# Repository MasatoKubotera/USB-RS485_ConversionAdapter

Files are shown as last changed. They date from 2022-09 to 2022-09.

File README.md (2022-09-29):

<html lang="en">
  <head>
    <meta charset="uft-8">
    <meta name="author" content="Masato Kubotera">
  </head>
  <body>
    <h1>USB-RS485 Conversion Adapter Ver. 2.1</h1>
    <h2>About USB-RS485 Conversion Adapter</h2>
    <p>
      The USB-RS485 Conversion Adapter converts communications from the USB interface to the RS-485 interface and can drive KONDO B3M series servo motors.<br>
      <br>
      Note that this is Ver. 2.1. For other versions, please refer to the following repositories.
      <ul>
        <li><a href="https://github.com/MasatoKubotera/USB-RS485_ConversionAdapter_ver2_0">USB-RS485 Conversion Adapter Ver. 2.0</a></li>
      </ul>
      <h2>About Ver. 2.1</h2>
      Ver. 2.1 has a switch and four indicator LEDs to turn the power supply for driving servo motors on and off on the board.
      <!--
      Ver.2.1では、サーボモーター駆動用の電源を基板上でON/OFFするためのスイッチと4つのインジケーターLEDを搭載しています。
      -->
      <table>
        <tr>
          <td>
            <a href="image/brd_top.png">
              <div align="center">
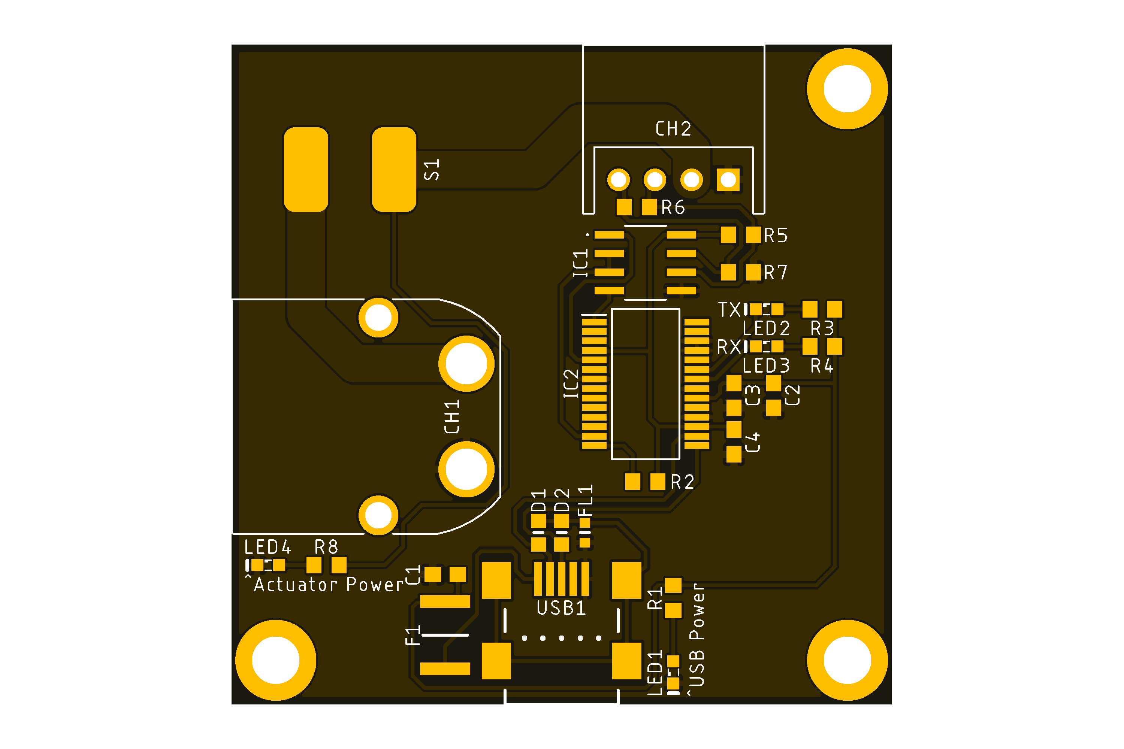
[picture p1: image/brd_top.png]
                
              </div>
            </a>
          </td>
          <td>
            <div align="center">
              
            </div>
          </td>
          <td>
            <div align="center">
              
            </div>
          </td>
        </tr>
        <tr>
          <td>
            <div align="center">
              PCB preview image
            </div>
          </td>
          <td>
            <div align="center">
              Actual PCB
            </div>
          </td> 
          <td>
            <div align="center">
              After component mounting
            </div>
          </td>   
        </tr>
      </table>
    </p>
    <h2>Repository Contents</h2>
    <p>
    <dl>
      <dt>\image</dt>
      <dd>PCB preview images and capture of design screen</dd>
      <dt>\libraries</dt>
      <dd>Libraries used in Autodesk Eagle design</dd>
      <dt>Schematic.pdf</dt>
      <dd>Circuit diagram of this product</dd>
      <dt>BOM.txt</dt>
      <dd>Parts lists output from design data</dd>
      <dt>.brd</dt>
      <dd>Board wiring design file by Autodesk Eagle</dd>
      <dt>.sch</dt>
      <dd>Schematic design file by Autodesk Eagle</dd>
      <dt>Gerber_data.zip</dt>
      <dd>Zip folder of Gerber format files for PCB manufacturing requests.</dd>
      <dt>LICENSE</dt>
      <dd>This is a license to use this product. Please confirm before use.</dd>
      <dt>.gitignore</dt>
      <dd>File to exclude cache files from management.</dd>
    </dl>
    </p>
    <h2>Documentation</h2>
      <p>
        <h3>BOM</h3>
          <table>
            <thead>
              <tr>
                <th> Eagle Design Parts # </th>
                <th> Q'ty </th>
                <th> Mfr. Product # </th>
                <th> Supplier </th>
                <th> Description </th>
              </tr>
            </thead>
            <tbody>
              <tr>
                <td> LED1, LED4 </td>
                <td> 2 </td>
                <td> 150060VS86000 </td>
                <td> <a href="https://www.mouser.jp/ProductDetail/Wurth-Elektronik/150060VS86000?qs=GedFDFLaBXGW9qOjzZ1Hmw%3D%3D">Mouser</a> </td>
                <td> Standard LEDs - SMD Green 2V 20mA 573nm 0603 </td>
              </tr>
              <tr>
                <td> LED2, LED3 </td>
                <td> 2 </td>
                <td> 150060YS75000 </td>
                <td> <a href="https://www.mouser.jp/ProductDetail/Wurth-Elektronik/150060YS75000?qs=LlUlMxKIyB0nKmwefHgtZw%3D%3D">Mouser</a> </td>
                <td> Standard LEDs - SMD Yellow 2V 20mA 590nm 0603 </td>
              </tr>
              <tr>
                <td> FL1 </td>
                <td> 1 </td>
                <td> BLM18SD220SN1D </td>
                <td> <a href="https://www.mouser.jp/ProductDetail/Murata-Electronics/BLM18SD220SN1D?qs=glnLrWX4TPq%2Fm8%2FdPQltLg%3D%3D">Mouser</a> </td>
                <td> Ferrite Beads 22 OHM 0603 </td>
              </tr>
              <tr>
                <td> R1, R3, R4 </td>
                <td> 3 </td>
                <td> RC0603FR-101KL </td>
                <td> <a href="https://www.mouser.jp/ProductDetail/YAGEO/RC0603FR-101KL?qs=EiqXWrxQq63MM0wzm69ZKg%3D%3D">Mouser</a> </td>
                <td> Thick Film Resistors - SMD 1 kOhms 100-200mW 1% 0603 </td>
              </tr>
              <tr>
                <td> R2 </td>
                <td> 1 </td>
                <td> RC0603FR-1310KL </td>
                <td> <a href="https://www.mouser.jp/ProductDetail/YAGEO/RC0603FR-1310KL?qs=EiqXWrxQq61KPbFOr8F%252BoA%3D%3D">Mouser</a> </td>
                <td> Thick Film Resistors - SMD 10 kOhms 100-200mW 1% 0604 </td>
              </tr>
              <tr>
                <td> R6 </td>
                <td> 1 </td>
                <td> RC0603FR-10120RL </td>
                <td> <a href="https://www.mouser.jp/ProductDetail/YAGEO/RC0603FR-10120RL?qs=EiqXWrxQq62dlPwl17gZoA%3D%3D">Mouser</a> </td>
                <td> Thick Film Resistors - SMD 120 Ohms 100-200mW 1% 0605 </td>
              </tr>
              <tr>
                <td> R5, R7 </td>
                <td> 2 </td>
                <td> RC0603FR-10680RL </td>
                <td> <a href="https://www.mouser.jp/ProductDetail/YAGEO/RC0603FR-10680RL?qs=kV3c90BOhBEc15QHcN6V1g%3D%3D">Mouser</a> </td>
                <td> Thick Film Resistors - SMD 680 Ohms 100-200mW 1% 0606 </td>
              </tr>
              <tr>
                <td> R8 </td>
                <td> 1 </td>
                <td> RC0603FR-102KL </td>
                <td> <a href="https://www.mouser.jp/ProductDetail/YAGEO/RC0603FR-102KL?qs=EiqXWrxQq61%2FIgp1yfYYog%3D%3D">Mouser</a> </td>
                <td> Thick Film Resistors - SMD 2 kOhms 100-200mW 1% 0607 </td>
              </tr>
              <tr>
                <td> C1 </td>
                <td> 1 </td>
                <td> GRM188B11H103KA01 </td>
                <td> <a href="https://www.google.com/search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">Akizuki</a> </td>
                <td> Multilayer Ceramic Capacitors SMD/SMT 0.01uF 50V 10% 0603 </td>
              </tr>
              <tr>
                <td> C2, C4 </td>
                <td> 2 </td>
                <td> GCM188L81H104K57 </td>
                <td> <a href="https://akizukidenshi.com/catalog/g/gP-16143/">Akizuki</a> </td>
                <td> Multilayer Ceramic Capacitors SMD/SMT 0.1uF 50V 10% 0603 </td>
              </tr>
              <tr>
                <td> C3 </td>
                <td> 1 </td>
                <td> C1608X5R1C475K080AE </td>
                <td> <a href="https://www.mouser.jp/ProductDetail/TDK/C1608X5R1C475K080AE?qs=j%252B1pi9TdxUYQJQlE8Tiuyw%3D%3D">Mouser</a> </td>
                <td> Multilayer Ceramic Capacitors SMD/SMT 4.7uF 16V 10% 0603 </td>
              </tr>
              <tr>
                <td> D1, D2 </td>
                <td> 2 </td>
                <td> CG0603MLC-05E </td>
                <td> <a href="https://www.mouser.jp/ProductDetail/Bourns/CG0603MLC-05E?qs=lDok7oSghXVLNKMK69q%252BFQ%3D%3D">Mouser</a> </td>
                <td> ESD Protectors 5V 0603 </td>
              </tr>
              <tr>
                <td> CH1 </td>
                <td> 1 </td>
                <td> XT60PW-M </td>
                <td> <a href="https://store.shopping.yahoo.co.jp/suzakulab/amass-xt60pw-m.html">Suzaku Lab.</a> </td>
                <td> DC Power Connector, Through Hole, Horizontal, Male, 30A 500V </td>
              </tr>
              <tr>
                <td> CH2 </td>
                <td> 1 </td>
                <td> S4B-XH-A(LF)(SN) </td>
                <td> <a href="https://akizukidenshi.com/catalog/g/gC-12842/">Akizuki</a> </td>
                <td> Connector Header Through Hole, Right Angle 4 position 2.5mm </td>
              </tr>
              <tr>
                <td> USB1 </td>
                <td> 1 </td>
                <td> MUSB-5B-NE-S175 </td>
                <td> <a href="https://akizukidenshi.com/catalog/g/gC-05843/">Akizuki</a> </td>
                <td> Mini USB Connector 5P B type, Female, SMT type, without standoff </td>
              </tr>
              <tr>
                <td> F1 </td>
                <td> 1 </td>
                <td> MF-MSMF050-2 </td>
                <td> <a href="https://www.mouser.jp/ProductDetail/Bourns/MF-MSMF050-2?qs=t3shhpq1i1DZ7OBD5kLNoA%3D%3D">Mouser</a> </td>
                <td> PTC Resettable Fuses 15V .5A-HD 100A MAX </td>
              </tr>
              <tr>
                <td> IC1 </td>
                <td> 1 </td>
                <td> ADM3078E<sup>*1</sup> </td>
                <td> <a href="https://www.mouser.jp/ProductDetail/Analog-Devices/ADM3078EARZ?qs=BpaRKvA4VqGLm2ZAElC2YA%3D%3D">Mouser</a> </td>
                <td> RS-485/RS-422 Transceiver (Half Duplex, 16 Mbps, DE/RE) </td>
              </tr>
              <tr>
                <td> IC2 </td>
                <td> 1 </td>
                <td> FT232RL </td>
                <td> <a href="https://akizukidenshi.com/catalog/g/gI-01739/">Akizuki</a> </td>
                <td> USB Interface IC USB to Serial UART </td>
              </tr>
              <tr>
                <td> S1 </td>
                <td> 1 </td>
                <td> DS-850K-S-ON </td>
                <td> <a href="https://akizukidenshi.com/catalog/g/gP-15740/">Akizuki</a> </td>
                <td> Rocker Switches 125VAC 5A </td>
              </tr>
            </tbody>
          </table>
          <strong>*1</strong> : Since the <a href="https://www.mouser.jp/ProductDetail/Analog-Devices/ADM3078EARZ?qs=BpaRKvA4VqGLm2ZAElC2YA%3D%3D">ADM3078E</a> from Analog Devices was not available at the time of fabrication, the <a href="https://akizukidenshi.com/catalog/g/gI-16211//">MAX3485ED</a> from HTC Korea was used as an alternative.
        <h3>PCB Fabrication</h3>
          PCB(Printed Circuit Board) manufacturing was outsourced to <a href="https://www.elecrow.com/pcb-manufacturing.html">Elecrow</a>.<br>
          The custom specifications are as follows.
          <ul>
            <li>Layer : 2 layers</li>
            <li>Dimensions : 45 x 45</li>
            <li>Different PCB Design : 1eg</li>
            <li>PCB Thickness : 1.6</li>
            <li>PCB Color : Black</li>
            <li>Surface Finish : HASL</li>
            <li>Castellated Hole : No</li>
            <li>Copper Weight : 1oz</li>
            <li>PCB Stencil : Stencil 10cm X 10cm no frame[Top]</li>
          </ul>
          The data used to order fabrication are as follows.
          <ul>
            <li>Eagle design rule : <a href="https://www.elecrow.com/download/Elecrow_PCB_eagle_rule.zip">Elecrow Eagle Design Rule</a></li>
            <li>Eagle CAM file : <a href="https://www.elecrow.com/download/Elecrow_Gerber_Generater_DrillAlign.zip">Elecrow CAM file</a></li>
            <li>Gerber format data : <a href="/Gerber_data.zip">Gerber_data.zip</a></li>
          </ul>
      </p>
    <h2>Contact</h2>
    <p>
    If you have any questions, please contact MasatoKubotera, the product's designer, by E-mail.<br>
    E-mail : <a href="mailto:masatokubotera06@yahoo.co.jp">masatokubotera06@yahoo.co.jp</a>
    </p>
    <h2>License Information</h2>
    <p>
      This product is open source.<br>
      Please review the <a href="/LICENSE">LICENSE file</a> for license information.<br>
      <br>
      <strong>USB-RS485 Conversion Adapter Ver. 2.1</strong> by Masato Kubotera is licensed under a <a href="http://creativecommons.org/licenses/by-nc-sa/4.0/">Creative Commons Attribution-NonCommercial-ShareAlike 4.0 International License</a>.
    </p>    
  </body>
</html>

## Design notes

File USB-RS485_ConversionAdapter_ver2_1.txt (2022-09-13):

Partlist exported from C:/Users/Masato/Desktop/USB-RS485_ConversionAdapter/USB-RS485_ConversionAdapter_ver2_1.sch at 2022/09/14 0:39

Qty Value          Device         Package        Parts                  Description                
4                  LEDSML0603     SML0603        LED1, LED2, LED3, LED4 LED                        
1   0.01u          C-USC0603      C0603          C1                     CAPACITOR, American symbol 
2   0.1u           C-USC0603      C0603          C2, C4                 CAPACITOR, American symbol 
1   10k            R-US_R0603     R0603          R2                     RESISTOR, American symbol  
1   120            R-US_R0603     R0603          R6                     RESISTOR, American symbol  
3   1k             R-US_R0603     R0603          R1, R3, R4             RESISTOR, American symbol  
1   2k             R-US_R0603     R0603          R8                     RESISTOR, American symbol  
1   4.7u           C-USC0603      C0603          C3                     CAPACITOR, American symbol 
2   680            R-US_R0603     R0603          R5, R7                 RESISTOR, American symbol  
1   ADM3078E       ADM3078E       ADM3078E       IC1                                               
1   BLM18SD220SN1D BLM18SD220SN1D BLM18SD220SN1D FL1                                               
2   CG0603MLC-05E  CG0603MLC-05E  CG0603MLC-05E  D1, D2                                            
1   DS-850K-S-ON   DS-850K-S-ON   DS-850K-S-ON   S1                                                
1   FT232RL        FT232RL        FT232RL        IC2                                               
1   MF-MSMF050     MF-MSMF050     MF-MSMF050     F1                                                
1   MINI_USB_B_SMD MINI_USB_B_SMD MINI_USB_B_SMD USB1                                              
1   S4B-XH-A       S4B-XH-A       S4B-XH-A       CH2                                               
1   XT60PW-M       XT60PW-M       XT60PW-M       CH1

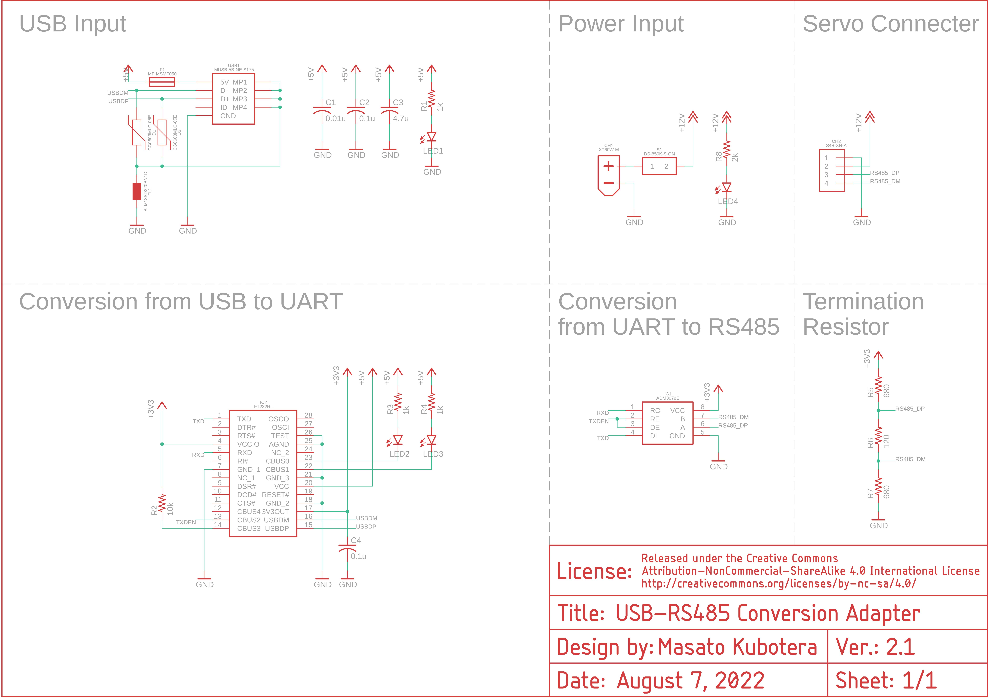
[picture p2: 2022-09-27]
image/sch.png

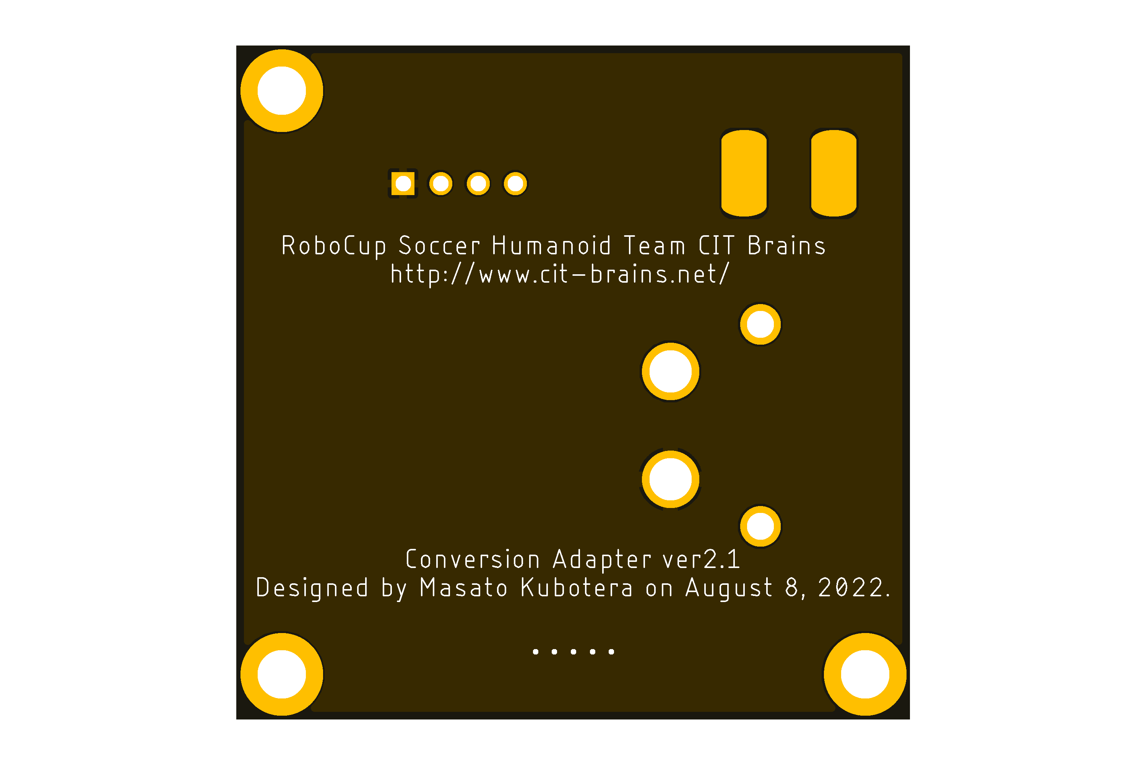
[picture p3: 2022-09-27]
image/brd_bottom.png

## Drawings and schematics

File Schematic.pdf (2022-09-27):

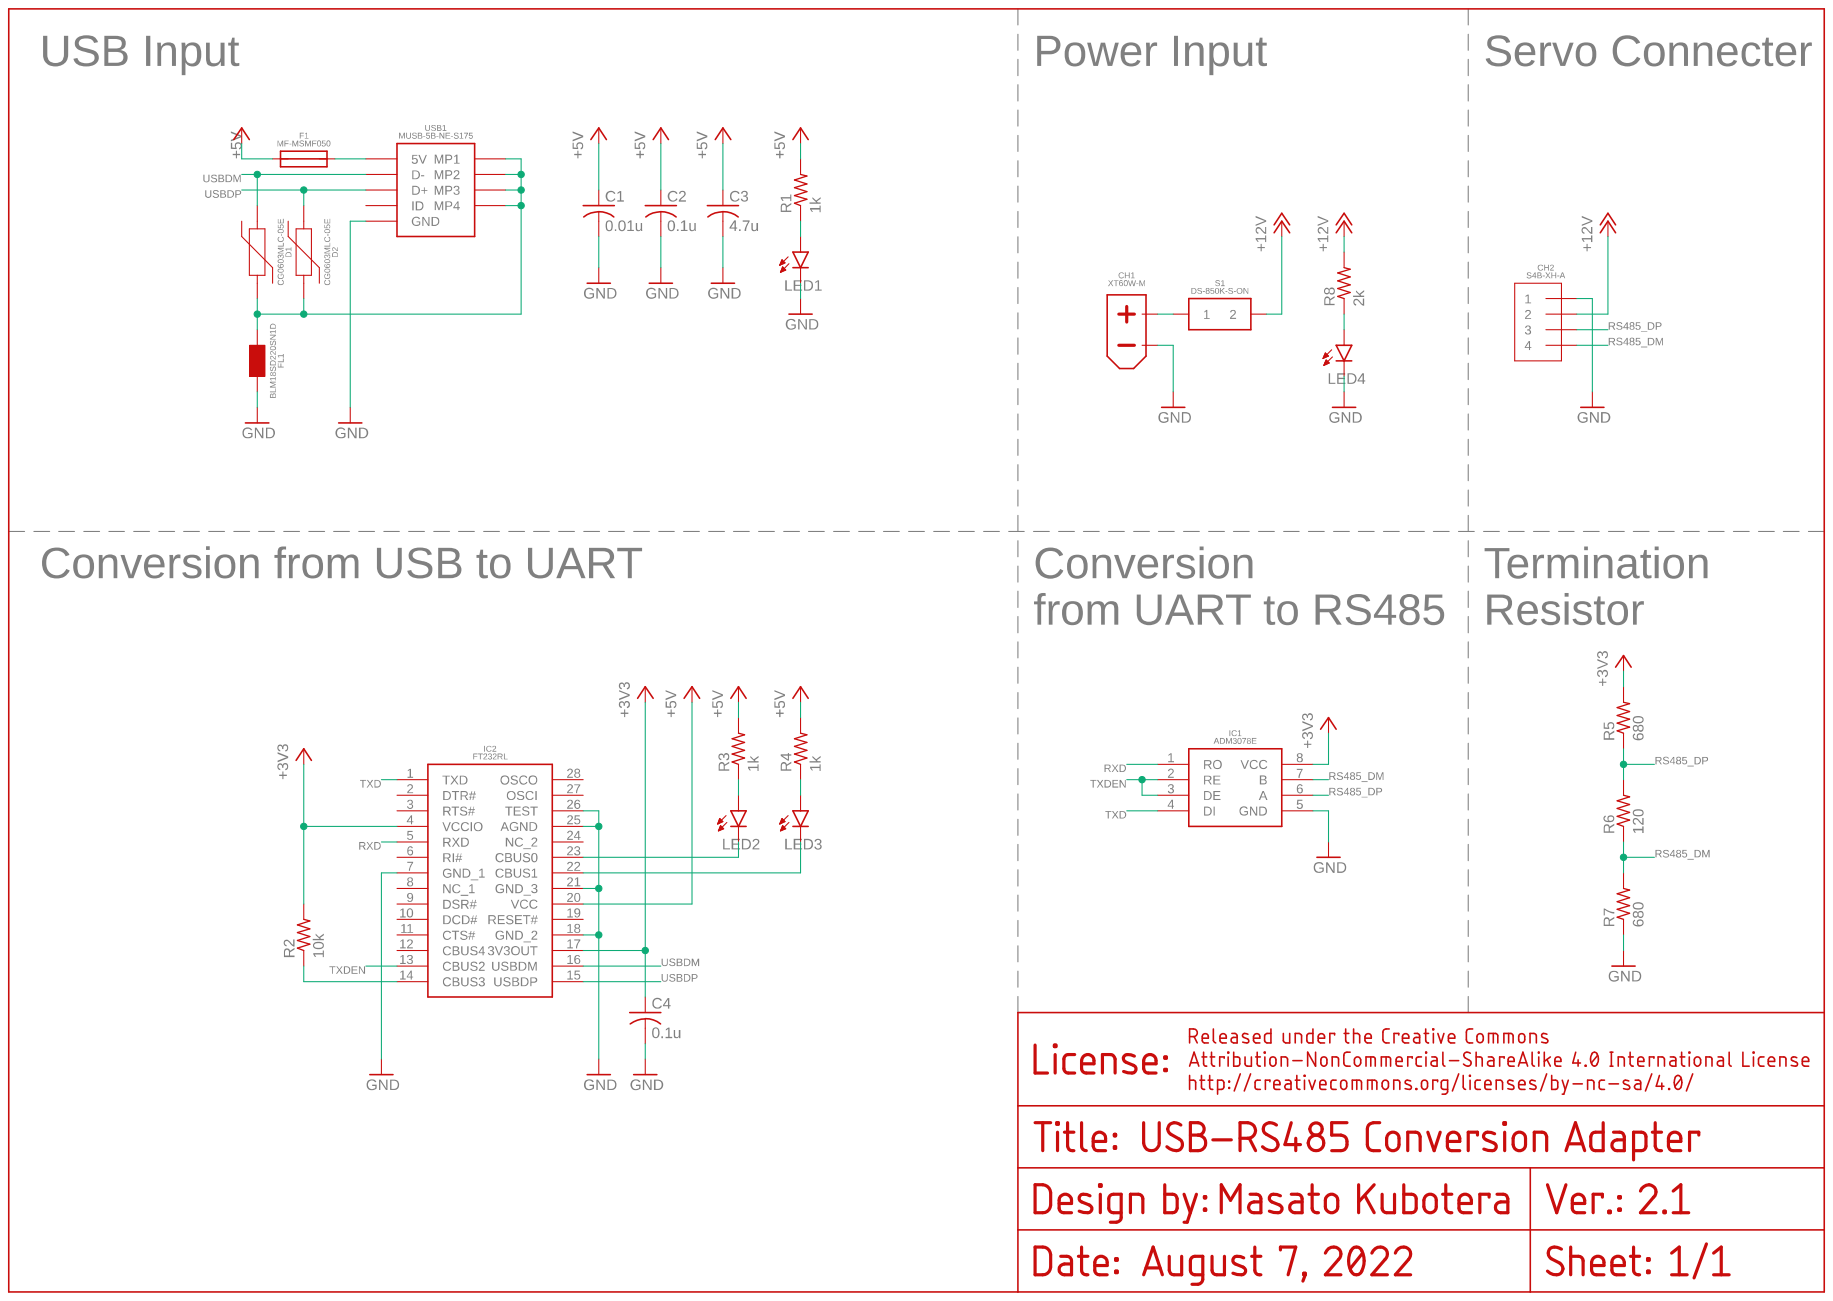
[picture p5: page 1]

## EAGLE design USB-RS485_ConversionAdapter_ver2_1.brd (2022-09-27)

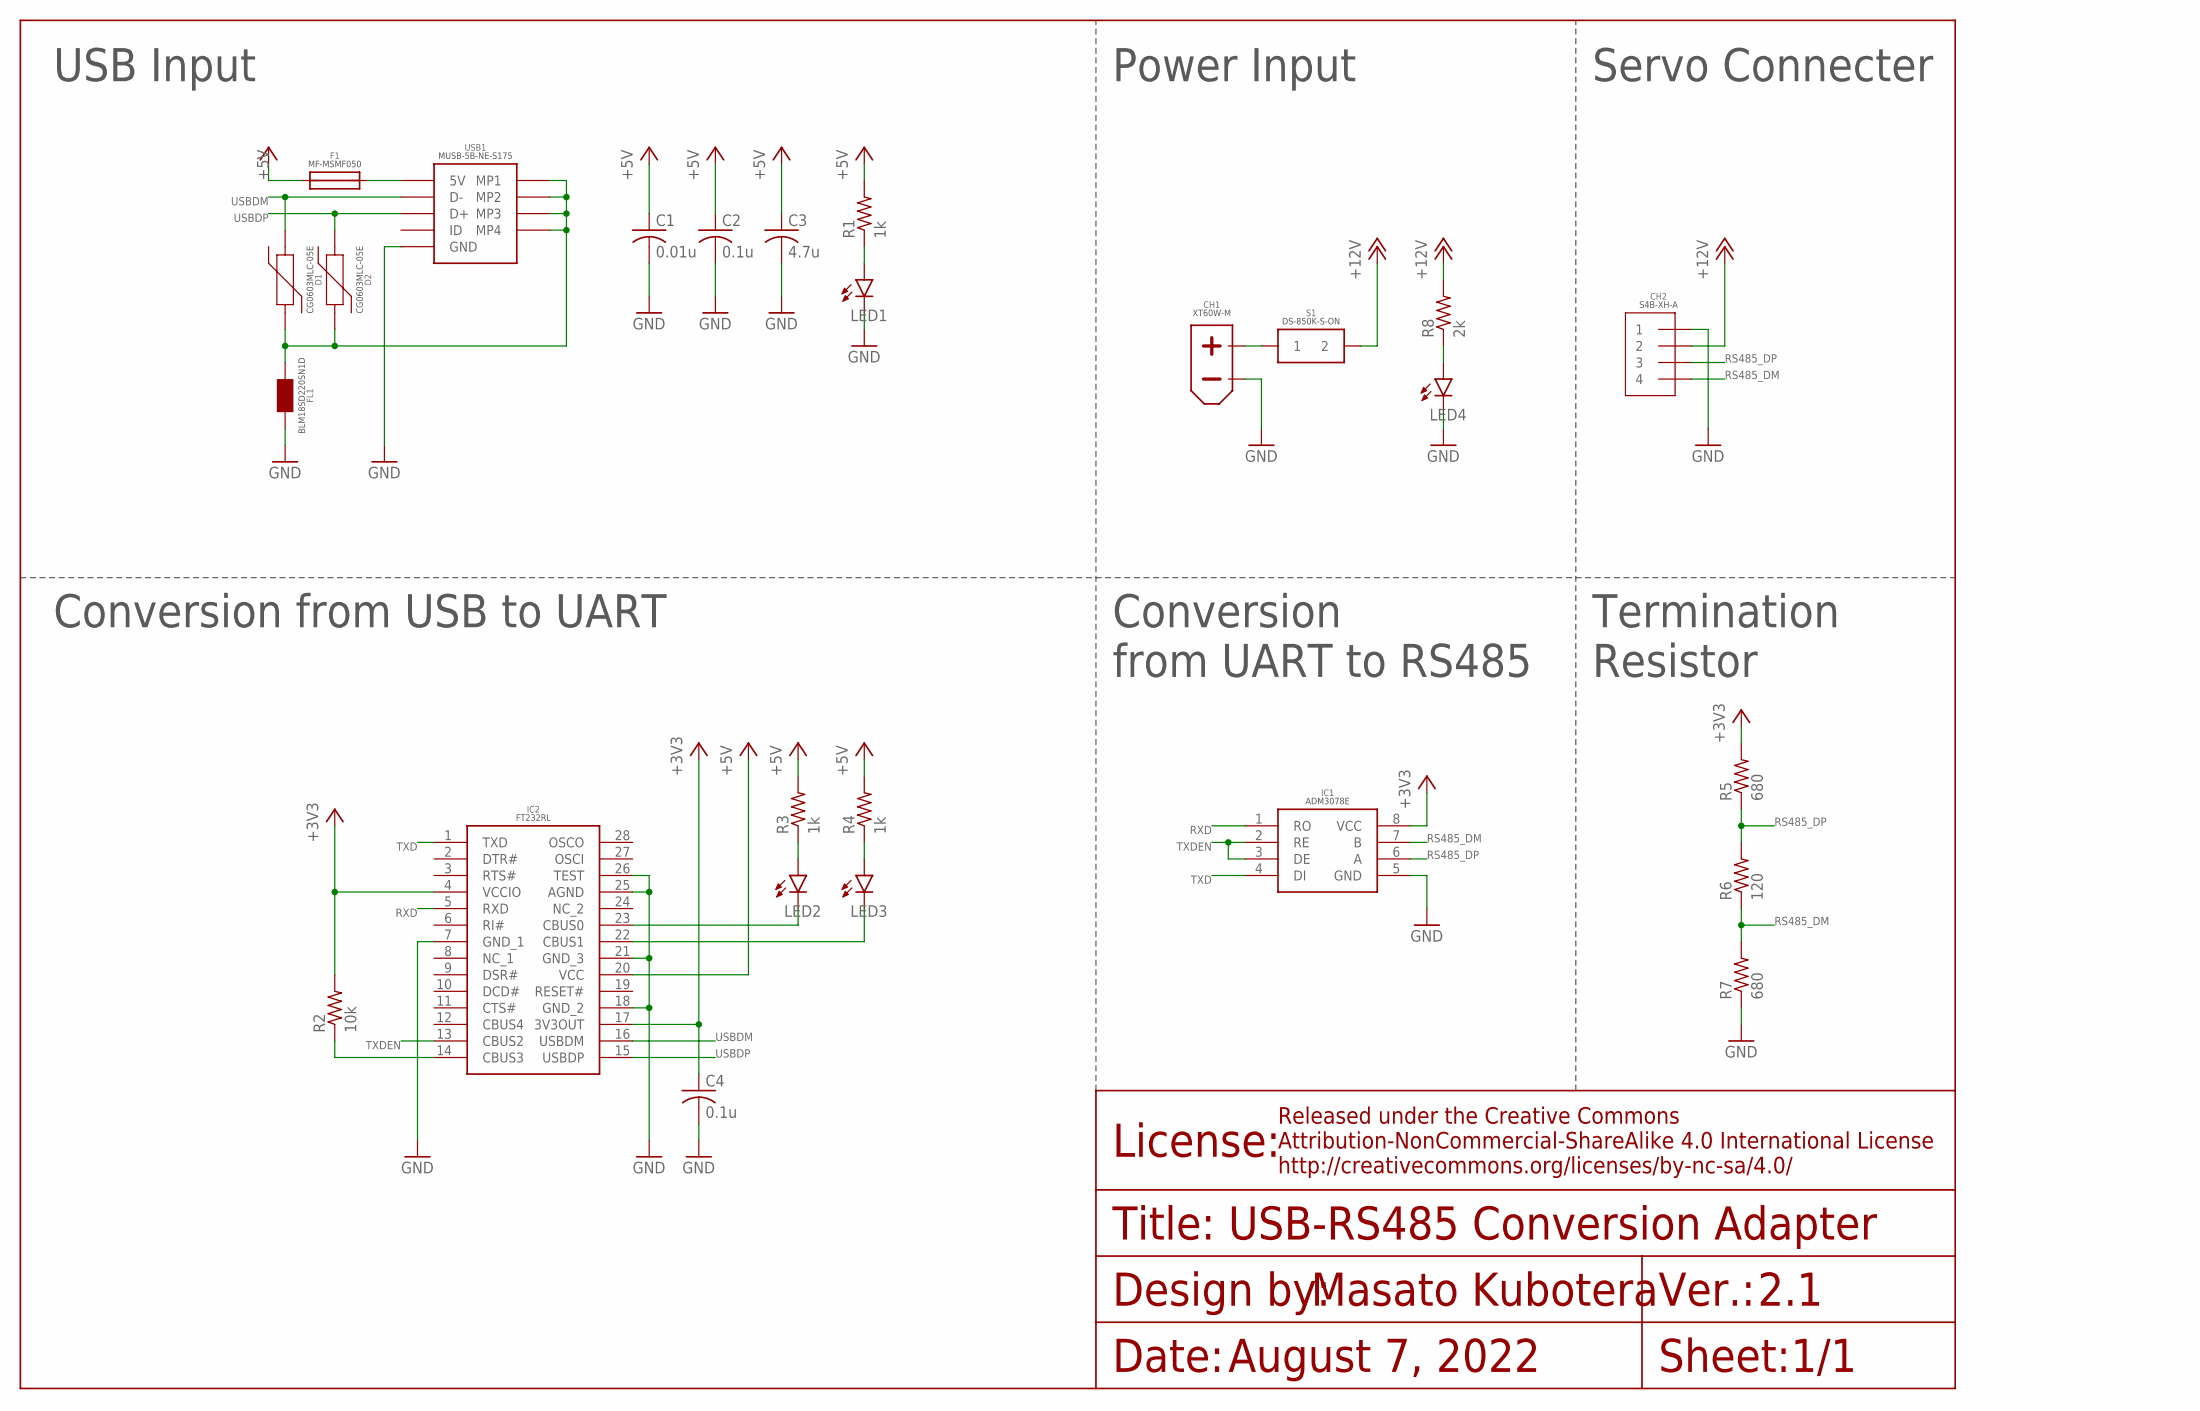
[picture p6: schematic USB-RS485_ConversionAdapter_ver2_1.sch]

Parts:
C1: 0.01u; C0603
C2, C4: 0.1u; C0603
C3: 4.7u; C0603
CH1: XT60PW-M
CH2: S4B-XH-A
D1, D2: CG0603MLC-05E
F1: MF-MSMF050
FL1: BLM18SD220SN1D
IC1: ADM3078E
IC2: FT232RL
LED1, LED2, LED3, LED4: LEDSML0603; SML0603
R1, R3, R4: 1k; R0603
R2: 10k; R0603
R5, R7: 680; R0603
R6: 120; R0603
R8: 2k; R0603
S1: DS-850K-S-ON
USB1: MINI_USB_B_SMD

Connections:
5V_LED: LED1.A, R1.1
12V_LED: LED4.A, R8.1
+3V3: C4.1, IC1.8 (VCC), IC2.4 (VCCIO), IC2.17 (3V3OUT), R2.2, R5.2
+5V: C1.1, C2.1, C3.1, F1.1, IC2.20 (VCC), R1.2, R3.2, R4.2
+12V: CH2.2, R8.2, S1.2B (2), S1.2T (2)
BEFORE_+12V: CH1.+, S1.1B (1), S1.1T (1)
B_FUSE_USB_MINI_B: F1.2, USB1.1 (5V)
CBUS0: IC2.23 (CBUS0), LED2.C
CBUS1: IC2.22 (CBUS1), LED3.C
CBUS3: IC2.14 (CBUS3), R2.1
GND: C1.2, C2.2, C3.2, C4.2, CH1.-, CH2.1, FL1.2, IC1.5 (GND), IC2.7 (GND_1), IC2.18 (GND_2), IC2.21 (GND_3), IC2.25 (AGND), IC2.26 (TEST), LED1.C, LED4.C, R7.1, USB1.5 (GND)
RS485_DM: CH2.4, IC1.7 (B), R6.1, R7.2
RS485_DP: CH2.3, IC1.6 (A), R5.1, R6.2
RXD: IC1.1 (RO), IC2.5 (RXD)
RXLED#: LED3.A, R4.1
TXD: IC1.4 (DI), IC2.1 (TXD)
TXDEN: IC1.2 (RE), IC1.3 (DE), IC2.13 (CBUS2)
TXLED#: LED2.A, R3.1
USBDM: D1.1, IC2.16 (USBDM), USB1.2 (D-)
USBDP: D2.1, IC2.15 (USBDP), USB1.3 (D+)
USB_MINI_B_SHIELD: D1.2, D2.2, FL1.1, USB1.MP1, USB1.MP2, USB1.MP3, USB1.MP4

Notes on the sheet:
2.1
1/1
August 7, 2022
USB-RS485 Conversion Adapter
USB Input
Power Input
Servo Connecter
Conversion from USB to UART
Conversion from UART to RS485
Termination Resistor

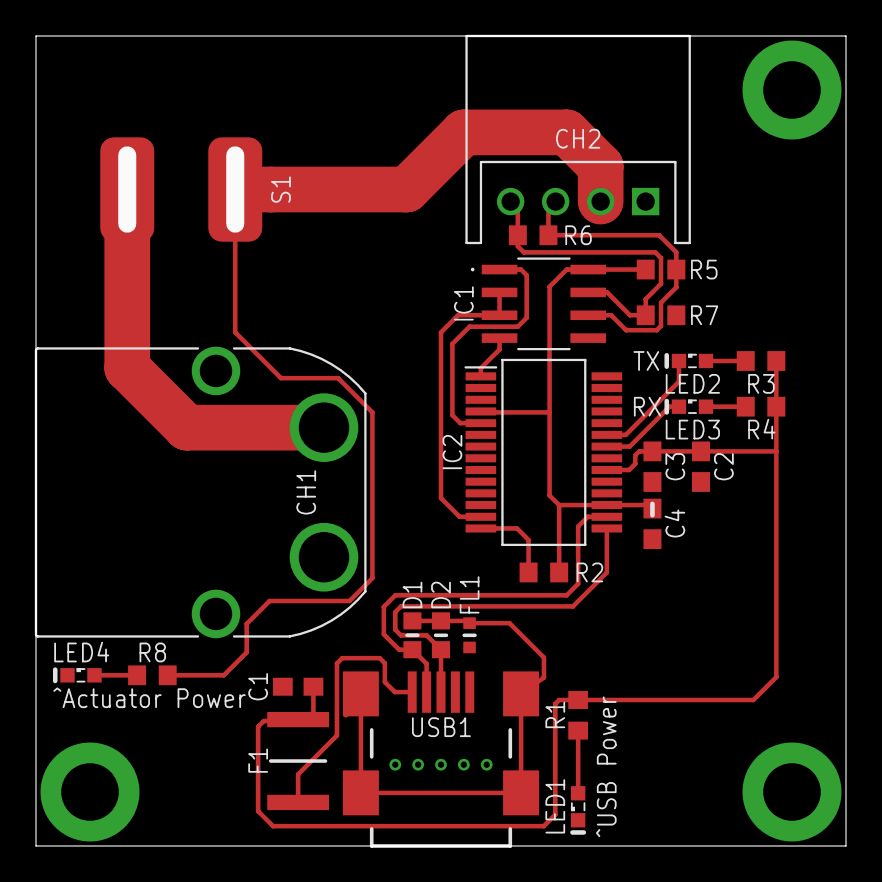
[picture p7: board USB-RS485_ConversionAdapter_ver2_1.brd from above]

Board: 2 copper layers, 45.0 x 45.0 mm, 26 parts (0 on the bottom side), 21 nets.

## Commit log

2022-09-13 Designed USB-RS485 Conversion Adapter
    [USB-RS485_ConversionAdapter_ver2_1.brd, USB-RS485_ConversionAdapter_ver2_1.sch]
2022-09-13 add BOM
2022-09-27 Update License and organize data
    [USB-RS485_ConversionAdapter_ver2_1.brd, USB-RS485_ConversionAdapter_ver2_1.sch]

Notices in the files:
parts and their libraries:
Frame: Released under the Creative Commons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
